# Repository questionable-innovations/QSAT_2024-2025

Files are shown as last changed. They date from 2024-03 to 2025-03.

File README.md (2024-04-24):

# APSS Reference PCBs
This is a collection of reference PCBs and Altium libraries for use within APSS.
The PSat folder includes a bunch of reference PCBs for use in PSat payloads.
The shared libraries folder includes a list of standardised parts for use within APSS. Many of these parts are available in the lab for breadboarding. You may of course use other components, but you will have to wait until they arrive before testing. 

## PSat Reference PCBs
A small collection of compatible PCBs and schematics for making a PSat payload with. See the separate readme in the folder for more details.

## APSS Altium Libraries
The libraries are split into flight-ready parts and prototyping parts. Prototyping parts are generally good parts that are cost-optimised, may not be automotive/military rated, and are not screened for CMOS latchups. These parts are useful for any non-critical design projects like PSat or ElevatorSat. 

Flight-ready parts are generally the highest performance parts that can be obtained for the role. They are automotive rated (or at least rated to automotive-like temperatures), checked for non-CMOS alternatives, etc. These should be used only for satellite-rated hardware like cubesat payloads, as some of these parts cost up to $20 each.

A General Components library also contains components like generic resistors, test points and pads, solder jumpers, etc.

## APSS Breadboard Adapters
A collection of small PCBs to use SMT parts on a breadboard.

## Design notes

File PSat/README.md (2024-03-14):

# PSat Reference PCBs
This is a collection of general-purpose PCBs for use in Psat payloads. This is designed to minimise the boilerplate that every PSat requires and allows you to specialise on whatever unique payload you choose.
Feel free to use this in your own payload. you could (in order of increasing complexity):

-   Use a previously assembled board, no work necessary
-   Assemble a board from an existing, unpopulated PCB and components (recommended)
-   Modify the PCB layout to suit your needs, print it, and assemble it
-   Use the schematic as a reference for your own custom design and layout
-   etc.

The original v1 and v2 designs were designed by Ross Porter (me), but I don’t expect this to be a static project: This is designed to be a community project, so once I’m gone I expect those with some electrical experience to take ownership, making adjustments or adding new features as required.

## Payload Slices
There are several boards that can be mixed and matched according to your needs. A brief description of each is given below. A full description can be found in the relevant subfolder's readme.

### Power Supply Unit (PSU)
The PSU slice is responsible for both charging the Lithium battery that powers your PSat, but also providing usable power rails for all your other devices. The board provides two step-down converters (default 1.8V and 3.3V) and one step-up converter (default 5V), all user-configurable during assembly. The battery can be charged using a USB-C or micro USB cable.

### Microcontroller (MCU)
The brains of the operation. A simple breakout board with programming header attached - never get stuck trying to program your microcontroller again! UART, SPI and I2C buses (among other pins) are broken out onto additional, optional stack headers for communication with other devices or slices.

### Beacon
Lost your PSat? Not any more. The beacon slice provides three locator devices:
 - A fully automatic audio beeper. This beeper produces a sharp chirp (100dB from 10cm away) every couple of seconds, which should be audible from about 50-100m away.
 - A 915MHz LoRa radio module. No radio license necessary, this radio can be used by a microcontroller to transmit a signal that you and a base station can use to triangulate the location of your payload. With a theoretical range of up to 2km (or 20km with a directional antenna on the base station), this radio is always an option. 
 - A self-contained GPS module. Use in combination with the LoRa radio and a microcontroller to broadcast your exact payload's GPS coordinates.

## Versioning
This project uses a form of semantic versioning to manage board interoperability:
ver X.Y.Z means version X, revision Y, patch Z.

The version X relates to both electrical and physical compatibility. Boards that share a major version X shall be physically and electrically compatible with eachother. If a change prevents a board from either physically mating (e.g. changing stack header location) or electrically interoperating (e.g. changing the location of the stack's ground pin) with other boards then this must be associated with an increase in version number.

The revision number Y relates to software-level changes. If a change does not affect physical or electrical interoperability but does require changing software (e.g. the location of two control pins have been swapped) then this must be associated with an increase in the revision number.

The patch number Z relates to internal bug fixes or additions to functionality. An increase in a board's patch number must be completely transparent to the wider stack, only adding additional functionality or solving issues/bugs internal to the board. Any already working stack shall continue to function (physically, electrically, and programmatically) even if one board receives a patch.

Examples:

PSU v1.0.0 <=/=> MCU v2.0.0

MCU v2.0.0 <=> Beacon v2.1.0, with software changes

MCU v2.2.0 <=> Beacon v2.2.37, with no software changes

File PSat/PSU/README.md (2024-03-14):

# Power Supply Unit (PSU)

See the documentation folder for version-specific readme's.

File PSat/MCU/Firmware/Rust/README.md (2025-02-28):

# How to use

Install Rust: https://www.rust-lang.org/learn/get-started

Install MSP430-GCC (installer or toolchain-only): https://www.ti.com/tool/MSP430-GCC-OPENSOURCE. Make sure it's on your PATH (or on Linux you can use `rustc-wrapper.sh`).

Then run the following commands:
`rustup install toolchain nightly`
`rustup component add rust-src --toolchain nightly`

You can now build the executable with `cargo build`. You can build in release mode with `cargo build --release`

(On Linux you will have to change the 'runner' line in `.cargo/config.toml` from `run.bat` to `run.sh`.)

# Flashing the board

Either use Code Composer Studio, under the 'flash' option click the dropdown and select the option that says 'select file to flash'. Point CCStudio to the binary at ./target/msp430-none-elf/release/apss_mcu_pcb_firmware

Alternatively, download uniflash from https://www.ti.com/tool/UNIFLASH#downloads. After installation open the program and either use auto-detect or input the board name (MSP430FR2355) manually. Click on 'standalone command-line' to generate a .zip file with all you need to flash the board.
Extract this folder so that dslite.bat is at `./uniflash/dslite.bat` within the project. 
After setting up uniflash you can flash the board by using `cargo run` or `cargo run --release`. (This also builds the project.)

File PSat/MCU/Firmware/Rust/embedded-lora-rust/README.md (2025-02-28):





# `embedded-lora`
`no-std`-compatible, opinionated drivers for some LoRa modems. Despite almost all modems supporting multiple radio
modulations, these drivers only implement LoRa. Furthermore, we currently only test the EU 868 MHz variants; other
variants may or may not work.

## `embedded-lora-rfm95`



dependency status (https://deps.rs/crate/embedded-lora-rfm95)

The [embedded-lora-rfm95](./rfm95/README.md) crate implements a driver for the popular RFM95 chips.

Currently supported features are:
- [x] Single RX
- [x] Single TX
- [x] Advanced LoRa modem configuration
- [x] SPI and modem register debugging
- [x] LoRa utils for AirTime computation

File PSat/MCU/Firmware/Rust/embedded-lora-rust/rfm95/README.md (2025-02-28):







dependency status (https://deps.rs/crate/embedded-lora-rfm95)

# `embedded-lora-rfm95`
A `no-std`-compatible, opinionated driver for the RFM95 LoRa modem. It only supports the LoRa mode, and has only been
tested with the EU 868 MHz ISM bands for now.

## Features
The crate supports the following optional `cargo` features:

### `fugit` (disabled by default)
The `fugit`-feature implements simple `From`/`Into`-conversions between the built-in frequency type and
[`fugit`'s](https://crates.io/crates/fugit) [`HertzU32` type](https://docs.rs/fugit/latest/fugit/type.HertzU32.html).
This is a comfort-feature only, and does not enable additional functionality.

### `debug` (disabled by default)
The `debug` feature enables some debug functionality, namely an SPI debug callback which can be used to log all SPI
transactions with the RFM95 modem, and provides some helper functions to dump the register state and FIFO contents. The
`debug` feature also disables the modem silicon revision check.

To use this feature, you __MUST__ implement this extern callback function in your crate (otherwise you'll get a cryptic
linker error):
```rust
extern "Rust" {
    /// A debug callback that is called for every SPI transaction
    /// 
    /// # About
    /// This function is called for every SPI transaction, where `operation` is the operation type (`0x00` for read,
    /// `0x80` for replace), `address` is the register address, and `input` and `output` are the values written and read
    /// respectively.
    fn embeddedrfm95_spidebug_AwiUzTRu(operation: u8, address: u8, input: u8, output: u8);
}
```

Example implementation:
```rust
/// The debug callback implementation for `embedded-rfm95`
#[no_mangle]
pub extern "Rust" fn embeddedrfm95_spidebug_AwiUzTRu(operation: u8, address: u8, input: u8, output: u8) {
    // Print the transaction to stdout
    println!("[SPI 0x{operation:02X} @[0x{address:02X}] tx:0x{input:02X} rx:0x{output:02X}");
}
```

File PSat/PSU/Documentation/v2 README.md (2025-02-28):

# Psat PSU PCB v2
The PSU PCB provides 1.8V, 3.3V, 5V rails and a raw battery voltage rail. The various supply rails can be always on, or controlled by software (see Functionality). USB-C and micro-USB connectors are present to charge the battery using a standard USB wall charger.
The supply rail voltages can be adjusted by changing the feedback resistor values. See the schematic for details.

## Functionality
### Controlling the Supply Rails
The PSU board offers two different control modes for each supply rail, controlled by the switches the S1 component: 
In the “ON” mode the relevant supply is always on. This is the simplest operating mode and no interaction with the enable pins are necessary. In this mode the enable pin is connected to Vraw via a 1.5k current-limiting resistor.

In the “OFF / SW control” mode, the supply defaults to off (pulled down by a 1Megohm resistor) but a microcontroller can enable the supply by pulling the enable pin high. If you want to programmatically enable a supply during operation you need to use this mode and connect your microcontroller to the enable pins on the header. See ‘Connections’ for the exact voltage(s) required to enable each supply.

*Note: If you configure S1 into the “ON” mode and have also connected the enable pin to a microcontroller, make sure to leave that GPIO pin as an input pin, as otherwise you will waste power through the 1.5k resistor.*

### USB charging
The board is capable of charging a lithium-ion battery by connecting a USB charger.
The two USB connectors (USB-C and micro-USB) are provided for convenience. DO NOT CHARGE USING BOTH CONNECTORS AT ONCE.
The battery will charge up to 800mA (USB power supply willing). This rate can be decreased by changing the value of R6, according to the datasheet of the battery charger.

### Disable while charging
The final S1 switch (labelled '*' on the PCB) is the 'supply disabled while charging' switch. It determines whether all the supply rails (including Vraw) are available while a USB cable is plugged in. The battery will of course charge faster if the load is disabled during charging. The BQ21040 battery charger IC states that it can also power loads during charging, so long as the charging time does not exceed 10 hours as a result, but this is not universally true for all charging ICs. When this switch is set to "ON" the load is disabled during charging. When it is set to "SW control" the supplies are enabled even while plugged in.

### 'Remove Before Flight’ Connector
RBF is a connector that controls whether the battery is connected to the PSU and stack. When the jumper is removed the entire stack has no power. When a jumper is placed across ABF (shorting the two pins) the battery is disconnected to the PSU and hence the stack. It is placed at a right-angle so that the jumper may be removed prior to launch through a hole in the exterior PSat shell.

## Connections
Header H1:

 - 1V8 -  1.8V step-down supply rail, capable of 2A output, battery not withstanding.
 - 3V3 -  3.3V step-down supply rail, capable of 2A output, battery not withstanding. *
 - 5V  -  5V step-up supply rail, capable of 2A output, battery not withstanding.
 - GND -  Common ground for all supply rails.
 - Vraw - Raw battery voltage. For a Li-ion battery this is between ~4.2V and ~3V.
 - 1V8_PG - Power good indicator for the 1.8V rail. Open-drain output: While the output voltage is more than 20% away from the regulation level this pin is pulled low, otherwise it is floating - you should attach this to a voltage source via a pullup resistor of your choosing.
 - 3V3_PG - Power good indicator for the 3.3V rail. Open-drain output: While the output voltage is more than 20% away from the regulation level this pin is pulled low,  otherwise it is floating - you should attach this to a voltage source via a pullup resistor of your choosing.
 - EN_1V8 - This pin may be pulled up above 1.5V to enable the 1.8V supply. The pin has a 1 Megohm pulldown resistor attached. When the equivalent S1 switch is in the "ON" position a 1.5k pullup resistor pulls this pin up to Vraw.
 - EN_3V3 - This pin may be pulled up above 1.5V to enable the 3.3V supply. The pin has a 1 Megohm pulldown resistor attached. When the equivalent S1 switch is in the "ON" position a 1.5k pullup resistor pulls this pin up to Vraw.
 - EN_5V - This pin may be pulled up above 1.2V to enable the 5V supply. The pin has a 1 Megohm pulldown resistor attached. When the equivalent S1 switch is in the "ON" position a 1.5k pullup resistor pulls this pin up to Vraw.

 \* *Note: This voltage is only stepped-down from the battery voltage, so if that goes below 3.3V this supply rail will as well. This means that across a full battery discharge this rail is nominally between 3.3V - 3.0V.*

## PCB Stacking
The PSat PSU is designed to be used in conjunction with either a single payload PCB (i.e. ‘2 PCB stack’) or in a stack of multiple PCBs (‘Multi-PCB stack’).

There are three types of 2.54mm pitch headers available in the lab, and which the PCB was designed with in mind:
Male headers with a 6mm mating length, 2.54mm insulation and a 3mm post.
Female headers with 8.5mm insulation and a 3mm post.
'Arduino female stacking headers' with 8.5mm of insulation, and 10.5mm posts.
### 2 PCB Stack
The simplest stack uses the supplied female header on the payload PSU and regular male headers on the payload board, pointed down. This produces a stack height of about 5mm.

The PSU is designed to go at the bottom of the stack (hence why the example payload has a cutout for the battery), but it can be moved up in the stack provided the battery can fit in the remaining space.

If a larger stack height is needed the standard female headers can be used to grant either ~8.5mm or ~11mm stack height (depending on whether the male pins are soldered with the plastic insulation between the PCBs or on the other side).

The stack height can be eliminated entirely if the male header is soldered such that the insulation is not between the two PCBs. Note that this would require the PSU PCB to be flipped (reversing the order of the header H1), as the underside of the PSU PCB must be used to mate against the payload (as no components on this side to interfere).

### Multi-PCB stack
The simplest stack uses the female stacking headers for each layer, except for the bottom which can use a standard female header, and the top which can use a standard male header (pointing down). This enforces a board-to-board stack height of 11mm between payload boards, and a stack height of around 5mm between the PSU board and the first payload board.

## Future changes
Maybe add a resettable fuse between the two USB connector’s bus voltages?

Maybe add a polyfuse to battery and each rail’s outputs

## Version History + Changelog
Version 2 - Not yet printed.
Move away from a centralised, fixed-size stack header to a flexible ‘only-what-is-necessary’ header: Rather than using a single 30-pin header with many unused pins, we use only a 10-pin header because the PSU PCB only needs 10 pins. Removed unused header pins as a result. PCBs further above in the stack can add additional headers adjacent to ours if necessary. 
Also switched to 2.54mm header due to a lack of 1.27mm ‘stacking’ headers. 2.54mm headers are also easier to route around, which actually makes it easier to add more pins to other PCBs in the stack if necessary, even though they’re bigger. 
Fixed Q1 by swapping pins 2 and 3. The mosfet body diode allowed Vbat to power the load even when the mosfet was (supposed to be) acting as an open circuit.
Added a resistor between Vraw and the EN_XYZ pins to prevent possible short circuit with microcontroller if switch is improperly configured

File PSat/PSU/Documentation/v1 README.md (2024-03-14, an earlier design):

# Psat PSU PCB v1
The PSU PCB provides 1.8V, 3.3V, 5V rails and a raw battery voltage rail. The various supply rails can be enabled, or controlled by software (see Functionality). USB-C and micro-USB connectors are present to charge the battery using a standard USB wall charger.
## Functionality
### Controlling the Supply Rails
The PSU board offers two different control modes for each supply rail, controlled by the switches on the S1 component: 
In the “ON” mode the relevant supply is always on. This is the simplest operating mode and no interaction with the enable pins are necessary. The enable pin is shorted to Vraw in this mode.

In the “OFF / SW control” mode, the supply defaults to off (pulled down by a 1Megohm resistor) but a microcontroller can enable the supply by pulling the enable pin high. If you want to programmatically enable a supply during operation you need to use this mode and connect your microcontroller to the enable pins on the header. See ‘Connections’ for the exact voltage(s) required to enable each supply.

**NOTE**: *If you have connected a microcontroller to the EN pins and plan to use it to control the supplies then a misconfigured S1 switch could result in your microcontroller trying to fight against an enable pin shorted to Vraw. Instead of using your GPIO as an output pin, we suggest setting it as an input pin and toggling the state of the internal pullup resistor to control the supplies. When the internal pullup is enabled it will form a voltage divider with the 1 Megohm external resistor, but it should be more than enough to activate the supply. In the case that S1 is misconfigured (i.e. in the “ON” mode, shorting the enable pin to Vraw) the pullup resistor will limit current to safe levels. See below.*

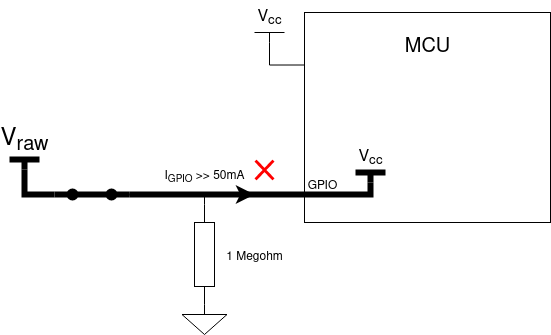
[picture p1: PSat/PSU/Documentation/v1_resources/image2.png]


A misconfiguration when controlling via an output pin can cause a short.

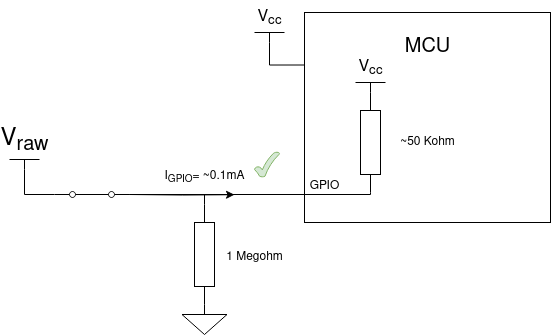
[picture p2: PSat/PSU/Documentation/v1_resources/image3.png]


Using an input pin with a pullup resistor enabled will limit current to a safe value even when misconfigured…

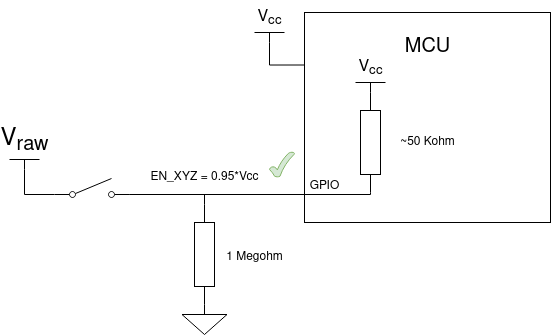
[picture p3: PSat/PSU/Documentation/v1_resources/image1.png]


…while still allowing control when correctly configured.

### USB charging
The two USB connectors (USB-C and micro-USB) are provided for convenience. **DO NOT PLUG IN TWO CABLES AT ONCE**.
The battery will charge at a rate of 800mA. This rate can be decreased by changing the value of R6, according to the datasheet of the battery charger.

### Disable while charging
The final S1 switch (labelled '*' on the PCB) is the 'supply disabled while charging' switch. It determines whether all the supply rails (including Vraw) are available while a USB cable is plugged in. The battery will of course charge faster if the load is disabled during charging. The BQ21040 battery charger IC states that it can also power loads during charging, so long as the charging time does not exceed 10 hours as a result, but this is not universally true for all charging ICs. When this switch is set to "ON" the load is disabled during charging. When it is set to "SW control" the supplies are enabled even while plugged in.

**NOTE**: *This feature does not work as intended on the v1 board. When set to ‘ON’ the payload continues to be powered with a voltage source about 0.7V lower than the battery voltage. It can either be fixed by mounting Q1 such that pins 2 and 3 are swapped, or if the functionality is not required then the ‘disable while charging’ switch can be left in the ‘OFF / SW control’ setting.*

### 'Attach Before Flight’ Connector
ABF is a connector that controls whether the battery is connected to the PSU and stack. When the jumper is removed the entire stack has no power. When a jumper is placed across ABF (shorting the two pins) the battery is connected to the PSU and hence the stack. It is placed at a right-angle so that the jumper may be inserted prior to launch through a hole in the exterior PSat shell.

## Connections
Header H1:

- 1V8 -  1.8V supply rail, capable of 2A output.
- 3V3 -  3.3V supply rail, capable of 2A output.
- 5V  -  5V supply rail, capable of 2A output.
- GND -  Common ground for all supply rails.
- Vraw - Raw battery voltage. For a Lithium battery this is between 3V to 4.2V.
- 1V8_PG - Power good indicator for the 1.8V rail. Open-drain output. It is is pulled up to Vraw when the output voltage is within 20% of the regulation level, otherwise it is low.
- 3V3_PG - Power good indicator for the 3.3V rail. Open-drain output. It is is pulled up to Vraw when the output voltage is within 20% of the regulation level, otherwise it is low.
- EN_1V8 - When the equivalent S1 switch is set to "SW control", this pin is pulled down with a 1 Megohm resistor. It may be pulled up above 1.5V to enable the 1.8V supply. When the equivalent S1 switch is in the "ON" position this pin is shorted to Vraw.
- EN_3V3 - When the equivalent S1 switch is set to "SW control", this pin is pulled down with a 1 Megohm resistor. It may be pulled up above 1.5V to enable the 3.3V supply. When the equivalent S1 switch is in the "ON" position this pin is shorted to Vraw.
- EN_5V  - When the equivalent S1 switch is set to "SW control", this pin is pulled down with a 1 Megohm resistor. It may be pulled up above 1.2V to enable the 5V supply. When the equivalent S1 switch is in the "ON" position this pin is shorted to Vraw.

## PCB Stacking
The PSat PSU is designed to be used in conjunction with a single payload PCB (or in a larger stack, provided you can find a female header with long enough posts).

The stack height with the connector given in the Altium project is 6.6mm, though this is just a placeholder. The connector is a board-to-board connector and is designed to be soldered in place, rendering the two PCBs permanently attached. We recommend finding another header, particularly if you want more than one payload PCB.

## Future changes
The S1 switches being inaccessible in small stack heights is inconvenient. Potentially replace with a right-angle connector?

Maybe add a resettable fuse between the two USB connector’s bus voltages?

Instead of S1 shorting the EN pin to Vraw, put a resistor (1k?) between potential MCUs and the EN line to prevent the possibility of shorts when misconfigured.

To check: The ‘power good’ indicators may need a pull-up resistor.

## PCB Version History
Version 1 - Initial design. Printed January 2024.

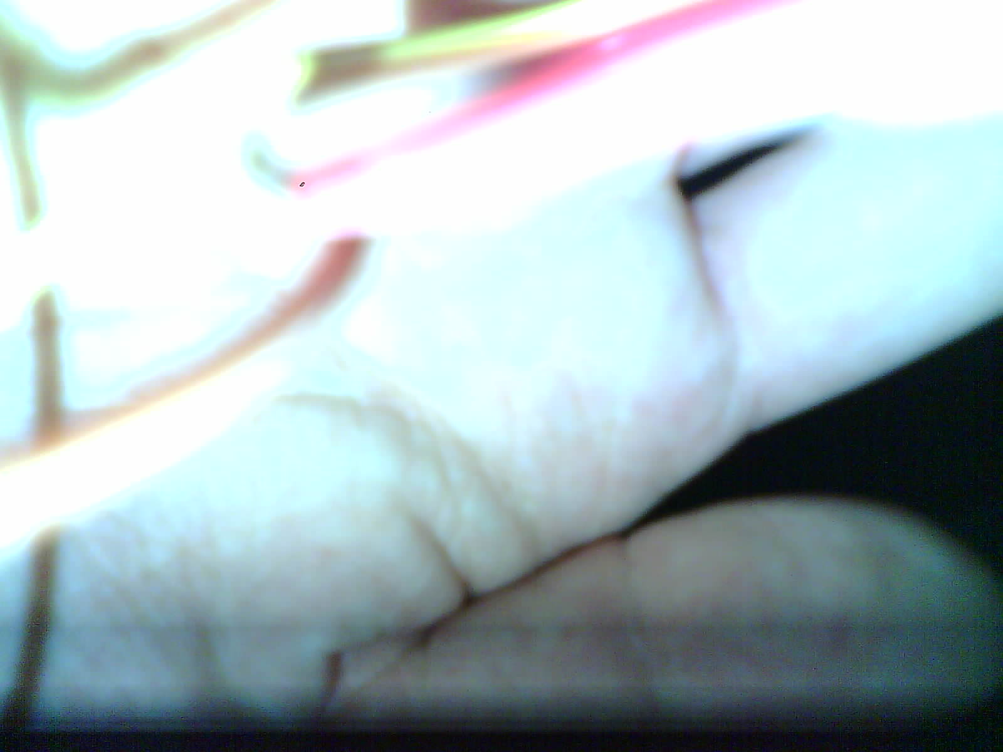
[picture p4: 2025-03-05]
ESPCAM/photos/picture45.jpg

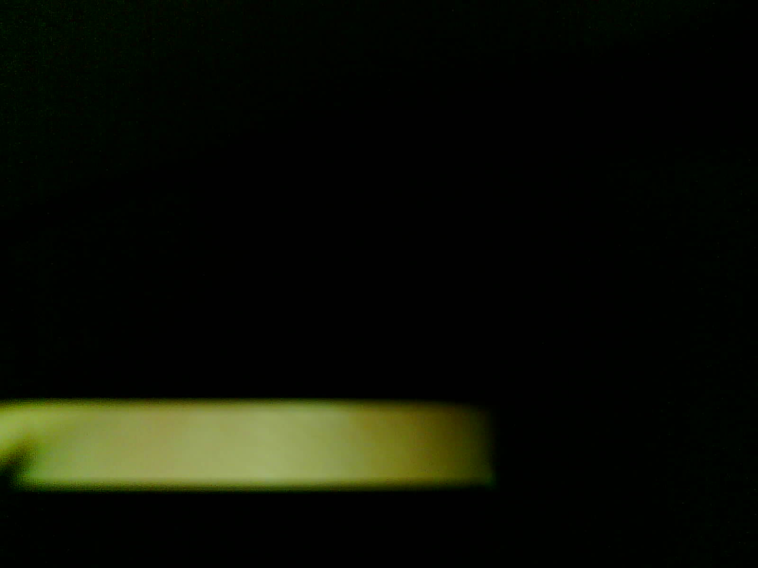
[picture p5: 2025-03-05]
ESPCAM/photos/picture4.jpg

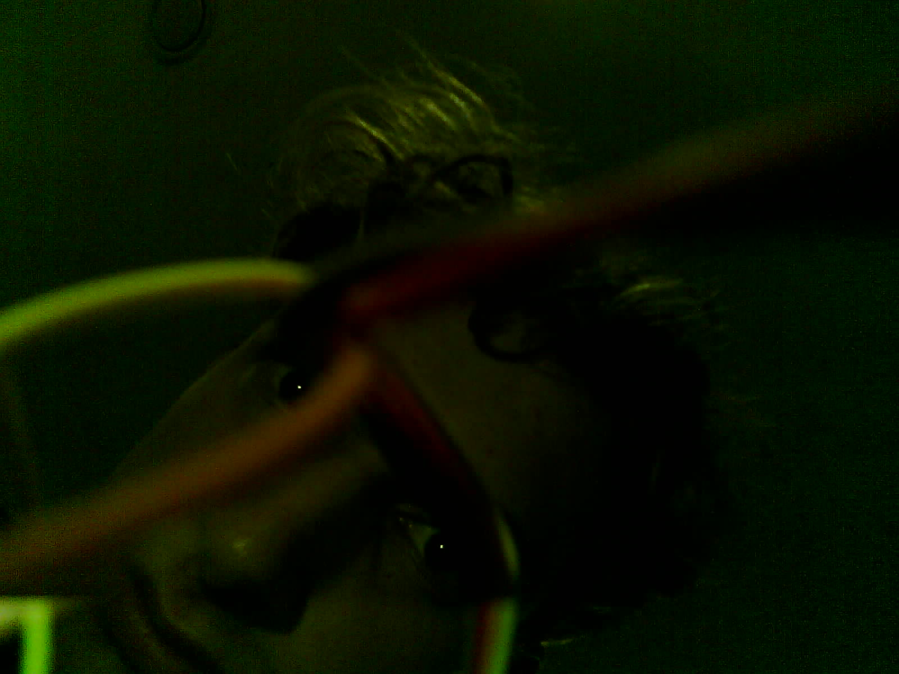
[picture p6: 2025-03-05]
ESPCAM/photos/picture10.jpg

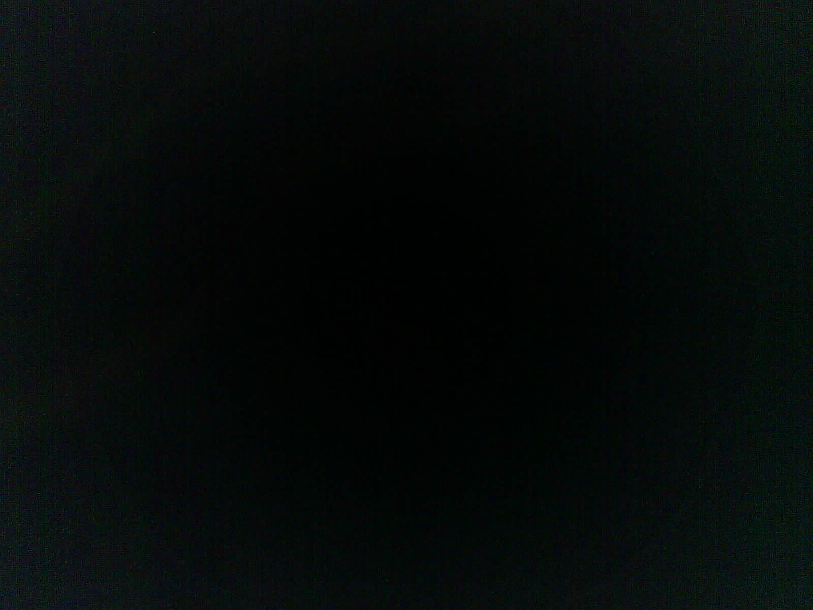
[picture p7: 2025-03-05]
ESPCAM/photos/picture37.jpg

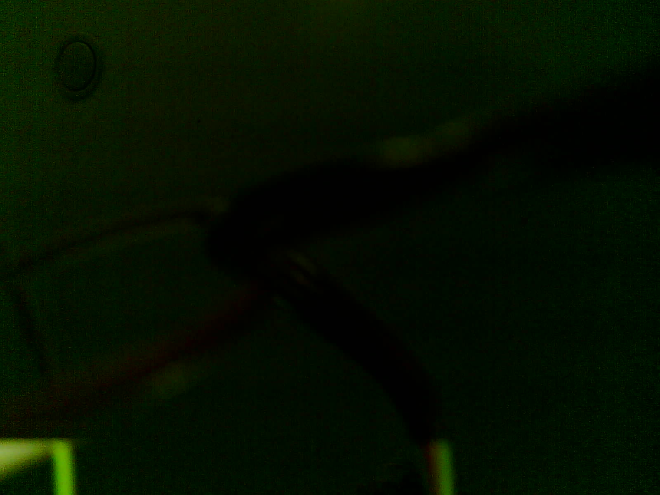
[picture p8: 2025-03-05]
ESPCAM/photos/picture9.jpg

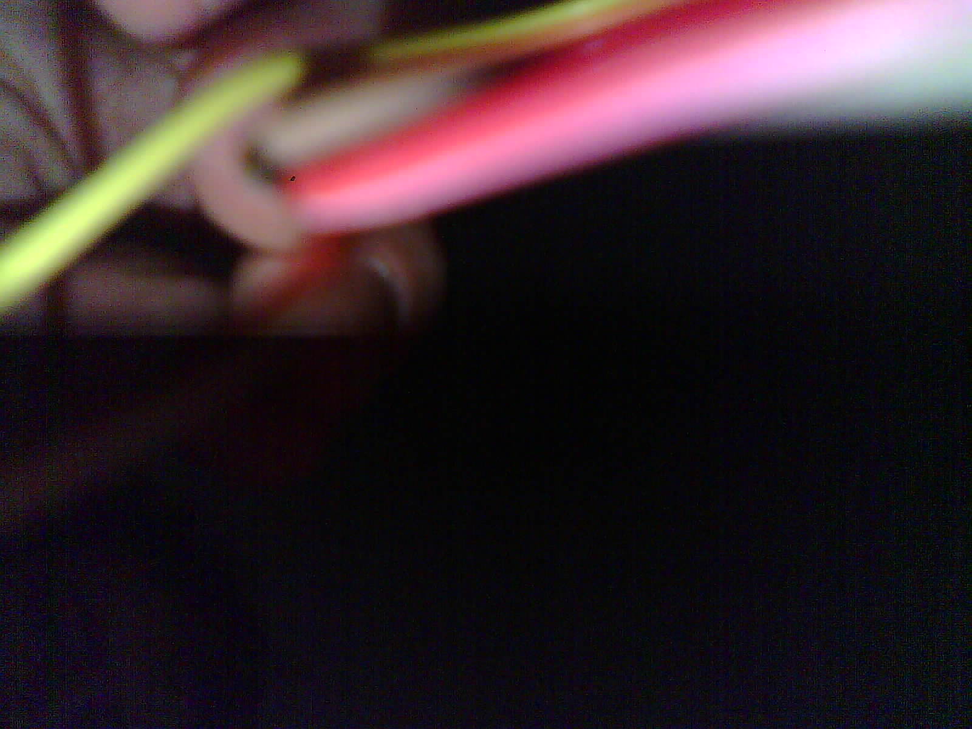
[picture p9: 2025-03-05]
ESPCAM/photos/picture39.jpg

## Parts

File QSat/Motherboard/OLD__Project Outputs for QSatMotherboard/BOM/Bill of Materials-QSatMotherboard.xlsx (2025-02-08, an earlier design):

Designator | Description | Comment | MF Part No. | Quantity | Supplier 1 | Supplier 1 Part No. | Package | APSS Standard Part
50k | Passive - Resistor Series, 0805, 0.5%, 10 - 1M, E24, 0.063W, 1/8W, ±25ppm/°C, -55°C ~ 155°C, 0805 (2012 Metric) | =Value |  | 1 | Digikey |  | 0805 | APSS Standard
ANT1 | Spring Antenna | HP-915-2.5A-9T | HP-915-2.5A-9T | 1
C1, C3, C4, C13, CIMU, CIMU1 | Generic Capacitor | 100nF | C0805C104K5RAC7800 | 6 | Digikey | 399-C0805C104K5RAC7800CT-ND | 0805
C2, C11, C12 | Passive - Capacitor, X5R, 22uF Max, 6.3V, 0805 (2012 Metric), ±20%, -55°C ~ 85°C. 8.8uF @ 5V | 22uF | C0805C226M9PACTU | 3 | Digikey | 399-C0805C226M9PAC7800CT-ND | 0402 | APSS Standard
C5 | Generic Capacitor | 1nF | 399-C0805C102J5GAC7800CT-ND | 1 | Digikey | 399-C0805C102J5GAC7800CT-ND | 0805
C10 | Passive - Capacitor, X7R, 220nF Max, 100V, 0805 (2012 Metric), ±10%, -55°C ~ 85°C. 200nF @ 10V, 110nF @ 50V, 55nF @ 100V | 220nF | C0805C224K1RAC7800 | 1 | Digikey | 399-C0805C224K1RAC7800CT-ND | 0805 | APSS Standard
D1, D4 | Diode - LED, 0603 | LTST-C190 Series | LTST-C190KGKT | 2 | Digikey |  | 0603 | APSS Standard
D2 | Diode - LED, 0603 | LTST-C190 Series | LTST-C190KSKT | 1 | Digikey |  | 0603 | APSS Standard
D3 | Diode - LED, 0603 | LTST-C190 Series | LTST-C190KAKT | 1 | Digikey |  | 0603 | APSS Standard
D5 | Diode - Low Reverse Leakage, 1.25 Vf @ 150 mA, 1 µA Reverse @ 75 V, SOD-123 | 1N4148W-TP | 1N4148W-TP | 1 | Digikey | 1N4148WTPMSCT-ND | SOD-123 | APSS Standard
H4 | Header - Picoblade 02-pin, TH, STR | 0530470210 | 0530470210 | 1 | Digikey | 530470210 |  | APSS Standard
J1 | No Description Available | PPTC081LFBN-RC |  | 1
J1b | Header - Picoblade 08-pin, SMT, RA | 0532610871 | 0532610871 | 1 | Digikey | WM7626CT-ND |  | APSS Standard
J2 | No Description Available |  |  | 1
J3, MH1, MH2 | Header - Picoblade 03-pin, TH, STR | 0530470310 | 0530470310 | 3 | Digikey | WM1732-ND |  | APSS Standard
LS1 | 8.5 mm, 5 Vo-p, 100 dB, Surface Mount (SMT), Magnetic Audio Transducer Buzzer | CMT-8504-100-SMT-TR | CMT-8504-100-SMT-TR | 1
OP1 | IC - Opamp, Precision, 2-Channel, Zero Drift, 270kHz GBWP, RRIO, 1.8V to 5.5V, -40 to 125, 8-MSOP | NCS2333DMR2G | NCS2333DMR2G | 1 | Digikey | 488-NCS2333DMR2GCT-ND | MSOP-8 0.65mm | APSS Standard
PWR | Header - Picoblade 02-pin, TH, STR | 0530470210 |  | 1 | Digikey | 530470210 |  | APSS Standard
Q1 | Transistor - MOSFET, N-Channel AS2312 | AS2312 | AS2312 | 1 | Digikey | 4530-AS2312CT-ND | SOT23-3 | APSS Standard
Q2 | Transistor - MOSFET, P-Channel SSM3J328R,LF | SSM3J328R,LF | SSM3J328R,LF | 1 | Digikey | SSM3J328RLFCT-ND | SOT23-3 | APSS Standard
R1 | Passive - Resistor Series, 0805, 5%, 100m - 22M, E24, 0.063W, 1/16W, ±200ppm/°C, -55°C ~ 155°C, 0805 (2012 Metric) | 47k | RMCF0805JT39K0 | 1 | Digikey |  | 0805 | APSS Standard
R2, R3, R4, R13, R16, R24, R25 | Passive - Resistor Series, 0805, 5%, 100m - 22M, E24, 0.063W, 1/16W, ±200ppm/°C, -55°C ~ 155°C, 0805 (2012 Metric) | 1k | RMCF0805JT1K00 | 7 | Digikey |  | 0805 | APSS Standard
R5 | Passive - Resistor Series, 0805, 5%, 100m - 22M, E24, 0.063W, 1/16W, ±200ppm/°C, -55°C ~ 155°C, 0805 (2012 Metric) | 47k | RMCF0805JT147K0 | 1 | Digikey |  | 0805 | APSS Standard
R6 | Passive - Resistor Series, 0805, 5%, 100m - 22M, E24, 0.063W, 1/16W, ±200ppm/°C, -55°C ~ 155°C, 0805 (2012 Metric) | 47k | RMCF0805JT47K0 | 1 | Digikey |  | 0805 | APSS Standard
R7 | Passive - Resistor Series, 0805, 5%, 100m - 22M, E24, 0.063W, 1/16W, ±200ppm/°C, -55°C ~ 155°C, 0805 (2012 Metric) | 4.7k | RMCF0805JT4K70 | 1 | Digikey |  | 0805 | APSS Standard
R8, R10, R27 | Passive - Resistor Series, 0805, 5%, 100m - 22M, E24, 0.063W, 1/16W, ±200ppm/°C, -55°C ~ 155°C, 0805 (2012 Metric) | 10k | RMCF0805JT4K70 | 3 | Digikey |  | 0805 | APSS Standard
R9, R11 | Passive - Resistor Series, 1206, 0.5%, 1R - 2M, E24+E96, 0.52W, 1/2W, ±25ppm/°C, -55°C ~ 155°C, 0805 (3216 Metric) | 2 | TNPW1206xxxxDE | 2 | Digikey |  | 0805 | APSS Standard
R12 | Passive - Resistor Series, 1206, 0.5%, 1R - 2M, E24+E96, 0.52W, 1/2W, ±25ppm/°C, -55°C ~ 155°C, 0805 (3216 Metric) | 50m | TNPW1206xxxxDE | 1 | Digikey |  | 0805 | APSS Standard
R14 | Passive - Resistor Series, 0805, 5%, 100m - 22M, E24, 0.063W, 1/16W, ±200ppm/°C, -55°C ~ 155°C, 0805 (2012 Metric) | 130 | RMCF0805JT1K00 | 1 | Digikey |  | 0805 | APSS Standard
R15 | Passive - Resistor Series, 0805, 5%, 100m - 22M, E24, 0.063W, 1/16W, ±200ppm/°C, -55°C ~ 155°C, 0805 (2012 Metric) | 150 | RMCF0805JT1K00 | 1 | Digikey |  | 0805 | APSS Standard
R17 | Passive - Resistor Series, 0805, 5%, 100m - 22M, E24, 0.063W, 1/16W, ±200ppm/°C, -55°C ~ 155°C, 0805 (2012 Metric) | 600 | RMCF0805JT1K00 | 1 | Digikey |  | 0805 | APSS Standard
R21, R22, R23 | Passive - Resistor Series, 0805, 5%, 100m - 22M, E24, 0.063W, 1/16W, ±200ppm/°C, -55°C ~ 155°C, 0805 (2012 Metric) | 180k | RMCF0805JT180K | 3 | Digikey |  | 0805 | APSS Standard
R26 | Passive - Resistor Series, 0805, 5%, 100m - 22M, E24, 0.063W, 1/16W, ±200ppm/°C, -55°C ~ 155°C, 0805 (2012 Metric) | 39k | RMCF0805JT39K0 | 1 | Digikey |  | 0805 | APSS Standard
S1 | Switch - Slide, SPDT, Straight, Break Before Make, 300mA, 6V | JS102011JCQN | JS102011JCQN | 1 | Digikey | CKN10721CT-ND |  | APSS Standard
U1 |  | MSP430FR2355TPT | MSP430FR2355TPT | 1 | Digikey | 296-50260-ND | LQFP-48
U2 | IMU ACCEL/GYRO I2C/SPI 14LGA | LSM6DSMTR |  | 1 |  |  | LGA-14L-DM00249496
U3 | CD-PA1616D GNSS patch antenna module | CD-PA1616D | CD-PA1616D | 1
U4 | LoRa transceiver | LORA127X-C1 | LORA127X-C1 | 1

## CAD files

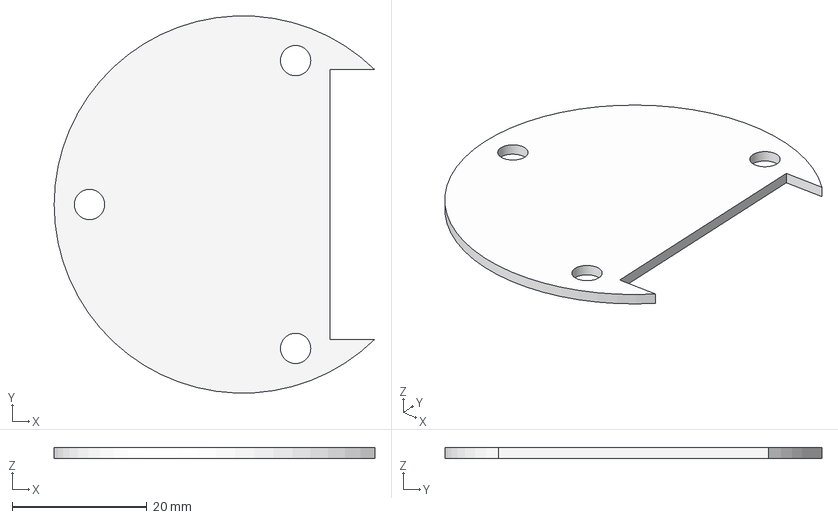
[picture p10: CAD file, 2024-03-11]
QSat/Motherboard/Payload Outline.step
47.6 x 56.0 x 1.60 mm

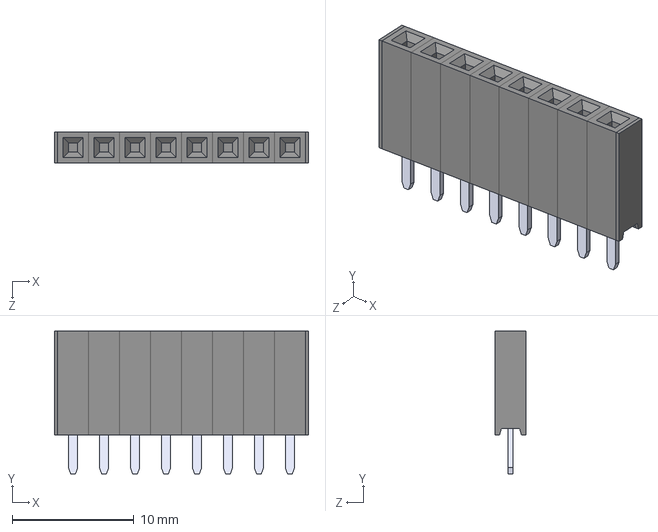
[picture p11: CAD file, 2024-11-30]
QSat/PartLib/PPTC081LFBN-RC/PPTC081LFBN-RC.STEP
20.8 x 11.7 x 2.54 mm
PPPC021LFBN-RC_C08
Pin - Tin x 8

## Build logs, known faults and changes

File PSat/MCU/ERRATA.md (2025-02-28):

# ERRATA
## 'Unknown device' when using 2-wire programming
Despite being the value recommended in the datasheet, C5 being 1nF is sometimes too high to allow programming when using 2-wire mode. Reducing C5 to 470pF solved the issue.

Affects: All versions

Fixed in version: TBD

## Reset pullup resistor value
Pullup resistor R1 is wrongly valued at 4.7k, the datasheet recommends 47k. No adverse affects noted. 

Affects v2.0.0 - v2.0.2

Fixed in: v2.0.3

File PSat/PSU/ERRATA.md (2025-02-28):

# ERRATA

## 'Remove/Attach Before Flight' header wrongly documented
The header that controls whether the payload switches on was originally an 'attach before flight' connector. This was changed to a 'remove before flight' header in v2.0.3, but the documentation was not updated until v2.0.6. The header behaves as an 'attach before flight' header from v2.0.0 to v2.0.2, and as a 'remove before flight' header from v2.0.3 onwards.

Affects: v2.0.3 - v2.0.5

Fixed in version: v2.0.6

## 'Disable while charging' feature does not work
The 'disable while charging' feature doesn't work correctly on the v1 PSU board. The toggle switch for this should be left in the 'Off / SW Control' position, unless the following fix is applied: Resolder Q1 such that pins 2 and 3 are swapped.

Affects: v1.*

Fixed in version: v2.0.0

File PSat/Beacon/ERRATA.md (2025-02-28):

# ERRATA

## GPS Enable Polarity
The documented functionality of the GPS enable transistor (Q2) is inverted: The documentation wrongly states that setting the gate of Q2 high enables the GPS. The gate of Q2 must be set *low* to enable the GPS. 

This also affects the default setting of SB7. The GPS defaults to being off with the default configuration, unless SB2 is shorted and GPS_EN is controlled as mentioned above.

Affects: v2.0.0 - v2.0.2

Fixed in version: v2.0.3

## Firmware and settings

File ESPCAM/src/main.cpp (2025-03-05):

#include "esp_camera.h"
#include "Arduino.h"
#include "FS.h"                // SD Card ESP32
#include "SD_MMC.h"            // SD Card ESP32
#include "soc/soc.h"           // Disable brownour problems
#include "soc/rtc_cntl_reg.h"  // Disable brownour problems
#include "driver/rtc_io.h"
#include <EEPROM.h>            // read and write from flash memory

// define the number of bytes you want to access
#define EEPROM_SIZE 16

// Pin definition for CAMERA_MODEL_AI_THINKER
#define PWDN_GPIO_NUM     32
#define RESET_GPIO_NUM    -1
#define XCLK_GPIO_NUM      0
#define SIOD_GPIO_NUM     26
#define SIOC_GPIO_NUM     27

#define Y9_GPIO_NUM       35
#define Y8_GPIO_NUM       34
#define Y7_GPIO_NUM       39
#define Y6_GPIO_NUM       36
#define Y5_GPIO_NUM       21
#define Y4_GPIO_NUM       19
#define Y3_GPIO_NUM       18
#define Y2_GPIO_NUM        5
#define VSYNC_GPIO_NUM    25
#define HREF_GPIO_NUM     23
#define PCLK_GPIO_NUM     22

int pictureNumber = 0;

void setup() {
  WRITE_PERI_REG(RTC_CNTL_BROWN_OUT_REG, 0); //disable brownout detector
 
  Serial.begin(115200);
  //Serial.setDebugOutput(true);
  //Serial.println();
  
  camera_config_t config;
  config.ledc_channel = LEDC_CHANNEL_0;
  config.ledc_timer = LEDC_TIMER_0;
  config.pin_d0 = Y2_GPIO_NUM;
  config.pin_d1 = Y3_GPIO_NUM;
  config.pin_d2 = Y4_GPIO_NUM;
  config.pin_d3 = Y5_GPIO_NUM;
  config.pin_d4 = Y6_GPIO_NUM;
  config.pin_d5 = Y7_GPIO_NUM;
  config.pin_d6 = Y8_GPIO_NUM;
  config.pin_d7 = Y9_GPIO_NUM;
  config.pin_xclk = XCLK_GPIO_NUM;
  config.pin_pclk = PCLK_GPIO_NUM;
  config.pin_vsync = VSYNC_GPIO_NUM;
  config.pin_href = HREF_GPIO_NUM;
  config.pin_sccb_sda = SIOD_GPIO_NUM;
  config.pin_sccb_scl = SIOC_GPIO_NUM;
  config.pin_pwdn = PWDN_GPIO_NUM;
  config.pin_reset = RESET_GPIO_NUM;
  config.xclk_freq_hz = 20000000;
  config.pixel_format = PIXFORMAT_JPEG; 
  
  if(psramFound()){
    config.frame_size = FRAMESIZE_UXGA; // FRAMESIZE_ + QVGA|CIF|VGA|SVGA|XGA|SXGA|UXGA
    config.jpeg_quality = 10;
    config.fb_count = 2;
  } else {
    config.frame_size = FRAMESIZE_SVGA;
    config.jpeg_quality = 12;
    config.fb_count = 1;
  }
  
  // Init Camera
  esp_err_t err = esp_camera_init(&config);
  if (err != ESP_OK) {
    Serial.printf("Camera init failed with error 0x%x", err);
    return;
  }
  
  //Serial.println("Starting SD Card");
  if(!SD_MMC.begin()){
    Serial.println("SD Card Mount Failed");
    return;
  }
  
  uint8_t cardType = SD_MMC.cardType();
  if(cardType == CARD_NONE){
    Serial.println("No SD Card attached");
    return;
  }

  // force flash off
  // pinMode(4, OUTPUT);
  // digitalWrite(4, LOW);
  // rtc_gpio_hold_en(GPIO_NUM_4);
  
  while (true) {
    camera_fb_t * fb = NULL;
    
    // Take Picture with Camera
    fb = esp_camera_fb_get();  
    if(!fb) {
      Serial.println("Camera capture failed");
      return;
    }
    // initialize EEPROM with predefined size
    EEPROM.begin(EEPROM_SIZE);
    pictureNumber = EEPROM.read(0) + 1;

    // Path where new picture will be saved in SD Card
    String path = "/picture" + String(pictureNumber) +".jpg";
    // String path = "/picture" + String(millis()) + ".jpg";

    fs::FS &fs = SD_MMC; 
    Serial.printf("Picture file name: %s\n", path.c_str());
    
    File file = fs.open(path.c_str(), FILE_WRITE);
    if(!file){
      Serial.println("Failed to open file in writing mode");
    } 
    else {
      file.write(fb->buf, fb->len); // payload (image), payload length
      Serial.printf("Saved file to path: %s\n", path.c_str());
      EEPROM.write(0, pictureNumber);
      EEPROM.commit();
    }
    file.close();
    esp_camera_fb_return(fb); 

    delay(1000); // Add a delay to avoid taking pictures too quickly
  }
  
}

void loop() {
  
}

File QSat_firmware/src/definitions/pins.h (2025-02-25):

#pragma once
#include <Arduino.h>

// 1	P1.2	I/O	LVCMOS	DVCC	OFF	TRUE	LoRa	SPI Master Out
// 2	P1.1	I/O	LVCMOS	DVCC	OFF	TRUE	LoRa	SPI Clock
// 8	P2.7	I/O	LVCMOS	DVCC	OFF	TRUE	LoRa	Lora Reset
// 9	P2.6	I/O	LVCMOS	DVCC	OFF	TRUE	LoRa	LoRa IRQ (DIO0)
// 10	P2.5	I/O	LVCMOS	DVCC	OFF	TRUE	LoRa	LoRa Configurable DIO1 (RadioLib wants it?)
// 11	P2.4	I/O	LVCMOS	DVCC	OFF	TRUE	ESP32 Cam	Hopefully will be used for OneWire commication with the ESPCam
// 12	P4.7	I/O	LVCMOS	DVCC	OFF	TRUE	Accelerometer	LSM6DSMTR I2C SCL
// 13	P4.6	I/O	LVCMOS	DVCC	OFF	TRUE	Accelerometer	LSM6DSMTR I2C SDA
// 23	P4.3	I/O	LVCMOS	DVCC	OFF	TRUE	GPS Module	GPS TX
// 24	P4.2	I/O	LVCMOS	DVCC	OFF	TRUE	GPS Module	GPS RX
// 27	P2.3	I/O	LVCMOS	DVCC	OFF	TRUE	GPS Module	GPS Enable
// 29	P2.1(RD)	I/O	LVCMOS	DVCC	OFF	TRUE	CamTrigServo	Send trigger servo PWM signal
// 30	P2.0	I/O	LVCMOS	DVCC	OFF	TRUE	CamTrigServo	Shutter reload servo PWM signal
// 31	P1.7	I/O	LVCMOS	DVCC	OFF	FALSE	JTAG, ESP32 Cam	Dual Use - It's a backup for the ESPCam com. If the DIY OneWire protocol doesn't work, we'll jank together the serial logs with communication to the ESPCam.
// 40	P5.3	I/O	LVCMOS	DVCC	OFF	TRUE	Current Sense	Analog current sense for servo controlling the shutter
// 41	P5.2	I/O	LVCMOS	DVCC	OFF	TRUE	LightSense	Read the photoresiste to detect leaving the capsual
// 42	P5.1	I/O	LVCMOS	DVCC	OFF	TRUE	Buzzer	PWM output for the buzzer - useful for finding capsual after rocket launch
// 43	P5.0	I/O	LVCMOS	DVCC	OFF	TRUE	Batt Manage	Default Sense Design
// 44	P3.3	I/O	LVCMOS	DVCC	OFF	TRUE	Status LED	LED1
// 45	P3.2	I/O	LVCMOS	DVCC	OFF	TRUE	Status LED	LED2
// 46	P3.1	I/O	LVCMOS	DVCC	OFF	TRUE	Status LED	LED3
// 47	P3.0	I/O	LVCMOS	DVCC	OFF	TRUE	Batt Manage	5V Enable
// 48	P1.3	I/O	LVCMOS	DVCC	OFF	TRUE	LoRa	SPI Master In

const int LoRa_SPI_SCK = P1_1;
const int LoRa_SPI_MOSI = P1_2;
const int LoRa_SPI_MISO = P1_3;
const int LoRa_Reset = P2_7;
const int LoRa_IRQ = P2_6;
const int LoRa_DIO1 = P2_5;


const int ESP32Cam_OneWire = P2_4;

const int LSM6DSMTR_SCL = P4_7;
const int LSM6DSMTR_SDA = P4_6;

const int GPS_TX = P4_3;
const int GPS_RX = P4_2;
const int GPS_Enable = P2_3;

const int CamTrigServo_Trigger = P2_1;
const int CamTrigServo_Reload = P2_0;

const int ESP32Cam_Backup = P1_7;

const int CurrentSense = P5_3;
const int LightSense = P5_2;
const int Buzzer = P5_1;
const int BattVoltageSense = P5_0;

const int StatusLED1 = P3_3;
const int StatusLED2 = P3_2;
const int StatusLED3 = P3_1;

const int BattManage_5VEnable = P3_0;

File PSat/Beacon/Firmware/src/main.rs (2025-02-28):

#![no_main]
#![no_std]

use embedded_hal::{digital::v2::*, spi::MODE_0};
use embedded_hal_compat::{eh1_0::delay::DelayNs, ForwardCompat};
use embedded_lora_rfm95::{lora::types::{Bandwidth, CodingRate, CrcMode, HeaderMode, Polarity, PreambleLength, SpreadingFactor, SyncWord}, rfm95::{Rfm95Driver, RFM95_FIFO_SIZE}};
use msp430::critical_section;
use msp430_rt::entry;
use msp430fr2355::{E_USCI_A0, E_USCI_A1, P2};
use msp430fr2x5x_hal::{
    clock::{ClockConfig, DcoclkFreqSel, MclkDiv, SmclkDiv}, delay::Delay, fram::Fram, gpio::{Batch, Output, Pin, Pin0, Pin1, Pin2}, hal::blocking::delay::DelayMs, pmm::Pmm, serial::SerialConfig, spi::SpiBusConfig, watchdog::Wdt
};

use core::{cell::RefCell, panic::PanicInfo, str};
#[panic_handler]
fn panic_handler(panic_info: &PanicInfo) -> ! {
    msp430::interrupt::disable();
    println!("Panic: {:?}", panic_info);
    loop { msp430::asm::barrier(); }
}

/// Standard printing. Fails to print if SERIAL hasn't been configured yet.
#[macro_export]
macro_rules! println {
    ($first:tt $(, $( $rest:tt )* )?) => {
        {
            critical_section::with(|cs| {
                let Some(ref mut serial) = *$crate::SERIAL.borrow_ref_mut(cs) else {loop{}};
                use core::fmt::Write;
                writeln!(serial, $first,  $( $($rest)* )*).ok();
            });
        }
    };
}

use msp430::interrupt::Mutex;
static SERIAL: Mutex<RefCell<Option< MySerial >>> = Mutex::new(RefCell::new(None));

// Red onboard LED should blink at a steady period.
#[entry]
fn main() -> ! {
    // Take peripherals and disable watchdog
    let regs = msp430fr2355::Peripherals::take().unwrap();
    let _wdt = Wdt::constrain(regs.WDT_A);

    // Configure GPIO
    let pmm = Pmm::new(regs.PMM);
    let port2 = Batch::new(regs.P2).split(&pmm);

    let mut red_led = port2.pin0.to_output();
    let mut blue_led = port2.pin1.to_output();
    let mut green_led = port2.pin2.to_output();

    red_led.set_high().ok();
    blue_led.set_high().ok();
    green_led.set_high().ok();

    let port1 = Batch::new(regs.P1).split(&pmm);
    let port4 = Batch::new(regs.P4).split(&pmm);
    let port5 = Batch::new(regs.P5).split(&pmm);

    let mut lora_reset = port5.pin3.to_output(); // Not actually connected...
    lora_reset.set_high().ok();
    let miso = port4.pin7.to_alternate1();
    let mosi = port4.pin6.to_alternate1();
    let sclk = port4.pin5.to_alternate1();
    let mut cs = port4.pin4.to_output();
    cs.set_high().ok();

    let tx_pin = port1.pin7.to_alternate1();

    // Configure clocks to get accurate delay timing
    let mut fram = Fram::new(regs.FRCTL);
    let (smclk, _aclk, mut delay) = ClockConfig::new(regs.CS)
        .mclk_dcoclk(DcoclkFreqSel::_8MHz, MclkDiv::_1)
        .smclk_on(SmclkDiv::_1)
        .freeze(&mut fram);

    let spi = SpiBusConfig::new(regs.E_USCI_B1, MODE_0, true)
        .use_smclk(&smclk, 32)
        .configure_with_software_cs(miso, mosi, sclk);

    let serial = SerialConfig::new(regs.E_USCI_A0, 
        msp430fr2x5x_hal::serial::BitOrder::LsbFirst, 
        msp430fr2x5x_hal::serial::BitCount::EightBits, 
        msp430fr2x5x_hal::serial::StopBits::OneStopBit, 
        msp430fr2x5x_hal::serial::Parity::NoParity, 
        msp430fr2x5x_hal::serial::Loopback::NoLoop, 
        9600)
        .use_smclk(&smclk)
        .tx_only(tx_pin);

    critical_section::with(|cs| {
        SERIAL.replace(cs, Some(MySerial(serial)));
    });
    //use core::fmt::Write;
    //let mut serial = MySerial(serial);
    println!("Serial init");

    lora_reset.set_low().ok();
    delay.delay_ms(1);
    lora_reset.set_high().ok();
    delay.delay_ms(6);

    let mut rfm95 = Rfm95Driver::new(spi.forward(), cs.forward(), lora_reset.forward(), MyDelay(delay)).unwrap();
    println!("RFM95 config success!");

    delay.delay_ms(1000);

    let lora_config = embedded_lora_rfm95::lora::config::Builder::builder()
        .set_bandwidth(Bandwidth::B7_8) // lowest bandwidth == longest range
        .set_coding_rate(CodingRate::C4_8) // Maximum error correction
        .set_crc_mode(CrcMode::Disabled)
        .set_frequency(915_000_000.into()) // Hz
        .set_header_mode(HeaderMode::Explicit)
        .set_polarity(Polarity::Normal)
        .set_preamble_length(PreambleLength::L8)
        .set_spreading_factor(SpreadingFactor::S10) // High SF == Best range
        .set_sync_word(SyncWord::PRIVATE);
    rfm95.set_config(&lora_config).unwrap();

    
    /*
    loop {
        println!("Beginning transmission...");
        transmit(&mut rfm95, b"Hello world!");
        println!("Transmission complete.");
        delay.delay_ms(1000);
    }*/
    
    loop {
        println!("Beginning recieve...");
        let mut recieve_buf = [0u8; RFM95_FIFO_SIZE];
        let packet = recieve(&mut rfm95, &mut recieve_buf);
        println!("Recieve ended.");
        println!("Packet: {}", str::from_utf8(packet).unwrap());
    }
    idle_loop(red_led, green_led, blue_led, delay);
}

type HorribleEmbeddedHalCompatRFM95Type = Rfm95Driver<embedded_hal_compat::Forward<msp430fr2x5x_hal::spi::SpiBus<msp430fr2355::E_USCI_B1>>, embedded_hal_compat::Forward<Pin<msp430fr2355::P4, msp430fr2x5x_hal::gpio::Pin4, Output>, embedded_hal_compat::markers::ForwardOutputPin>>;

fn recieve<'b>(rfm95: &mut HorribleEmbeddedHalCompatRFM95Type, buf: &'b mut [u8; RFM95_FIFO_SIZE]) -> &'b [u8] {
    let size;
    'outer: loop {
        let max_timeout = rfm95.rx_timeout_max().unwrap();
        rfm95.start_rx(max_timeout).unwrap();

        
        'inner: loop {
            match rfm95.complete_rx(buf) {
                Ok(Some(n)) => {size = n; break 'outer;},
                Ok(None) => continue,
                Err(_) => break 'inner,
            };
        };

    }
    &buf[0..size]
}

fn transmit(rfm95: &mut HorribleEmbeddedHalCompatRFM95Type, data: &[u8]) {
    rfm95.start_tx(data).unwrap();
    let mut result = rfm95.complete_tx();
    while let Ok(None) = result {
        result = rfm95.complete_tx();
    }
}

fn idle_loop(mut red_led: Pin<P2, Pin0, Output>, mut green_led: Pin<P2, Pin2, Output>, mut blue_led: Pin<P2, Pin1, Output>, mut delay: Delay) -> ! {
    loop {
        const LED_DELAY_MS: u16 = 50; // ms
        // Returns a `Result` because of embedded_hal, but the result is always `Ok` with MSP430 GPIO.
        // Rust complains about unused Results, so we 'use' the Result by calling .ok()
        red_led.set_low().ok();
        delay.delay_ms(LED_DELAY_MS);

        green_led.set_low().ok();
        delay.delay_ms(LED_DELAY_MS);

        blue_led.set_low().ok();
        delay.delay_ms(LED_DELAY_MS);

        red_led.set_high().ok();
        delay.delay_ms(LED_DELAY_MS);

        green_led.set_high().ok();
        delay.delay_ms(LED_DELAY_MS);

        blue_led.set_high().ok();
        delay.delay_ms(LED_DELAY_MS);
    }
}
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

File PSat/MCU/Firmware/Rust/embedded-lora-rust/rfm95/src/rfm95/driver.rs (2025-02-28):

//! RFM95 driver for LoRa operations

use crate::lora::airtime;
use crate::lora::config::Config;
use crate::lora::types::*;
use crate::rfm95::connection::Rfm95Connection;
use crate::rfm95::registers::*;
use crate::rfm95::RFM95_FIFO_SIZE;
use core::cmp;
use core::fmt::{Debug, Formatter};
use core::time::Duration;
use embedded_hal::delay::DelayNs;
use embedded_hal::digital::OutputPin;
use embedded_hal::spi::SpiBus;

/// Raw SPI command interface for RFM95
pub struct Rfm95Driver<Bus, Select>
where
    Bus: SpiBus,
    Select: OutputPin,
{
    /// The SPI connection to the RFM95 radio
    spi: Rfm95Connection<Bus, Select>,
}
impl<Bus, Select> Rfm95Driver<Bus, Select>
where
    Bus: SpiBus,
    Select: OutputPin,
{
    /// Supported silicon revisions for compatibility check
    #[cfg(not(feature = "debug"))]
    const SUPPORTED_SILICON_REVISIONS: [u8; 2] = [0x11, 0x12];
    /// The frequency divider to compute the frequency in milli-hertz
    const FREQUENCY_DIVIDER_MILLIHZ: u64 = 61_035;
    /// The threshold for switching between low-frequency mode (below 525 MHz) and high frequency mode (above 779 MHz)
    const HIGH_FREQUENCY_THRESHOLD: Frequency = Frequency::hz(652_000_000);

    /// The register value to put the device to LoRa mode
    const REG_OPMODE_LONGRANGEMODE_LORA: u8 = 0b1;
    /// The register value to set the shared registers to LoRa mode
    const REG_OPMODE_ACCESSSHAREDREG_LORA: u8 = 0b0;
    /// The pre-assembled register value for the operation mode register to put the device to sleep
    const REG_OPMODE_MODE_SLEEP: u8 = 0b000;
    /// The pre-assembled register value for the operation mode register to go into standby during LoRa mode
    const REG_OPMODE_MODE_STANDBY: u8 = 0b001;
    /// The pre-assembled register value for the operation mode register to start a single LoRa TX transmission
    const REG_OPMODE_MODE_TXSINGLE: u8 = 0b011;
    /// The pre-assembled register value for the operation mode register to start a single LoRa RX reception
    const REG_OPMODE_MODE_RXSINGLE: u8 = 0b110;

    /// Creates a new raw SPI command interface for RFM95
    ///
    /// # Blocking
    /// This function blocks for at least `11ms` plus additional time for the modem transactions. If you have tight
    /// scheduling requirements, you probably want to initialize this driver before entering your main event loop.
    ///
    /// # Important
    /// The RFM95 modem is initialized to LoRa-mode and put to standby. All other configurations are left untouched, so
    /// you probably want to configure the modem initially (also see [`Self::set_config`]).
    pub fn new<R, T>(bus: Bus, select: Select, mut reset: R, mut timer: T) -> Result<Self, &'static str>
    where
        R: OutputPin,
        T: DelayNs,
    {
        // Pull reset to low and wait until the reset is triggered
        reset.set_low().map_err(|_| "Failed to pull reset line to low")?;
        timer.delay_ms(1);

        // Pull reset to high again and give the chip some time to boot
        reset.set_high().map_err(|_| "Failed to pull reset line to high")?;
        timer.delay_ms(10);

        // Validate chip revision to assure the protocol matches
        let mut wire = Rfm95Connection::init(bus, select);
        #[cfg(not(feature = "debug"))]
        {
            // Get chip revision
            let silicon_revision = wire.read(RegVersion)?;
            let true = Self::SUPPORTED_SILICON_REVISIONS.contains(&silicon_revision) else {
                // Raise an error here since other revisions may be incompatible
                return Err("Unsupported silicon revision");
            };
        }

        // Go to sleep, switch to LoRa and enter standby
        wire.write(RegOpModeMode, Self::REG_OPMODE_MODE_SLEEP)?;
        wire.write(RegOpModeLongRangeMode, Self::REG_OPMODE_LONGRANGEMODE_LORA)?;
        wire.write(RegOpModeMode, Self::REG_OPMODE_MODE_STANDBY)?;
        wire.write(RegOpModeAccessSharedReg, Self::REG_OPMODE_ACCESSSHAREDREG_LORA)?;

        // Set TX and RX base address to 0 to use the entire available FIFO space, and the power amplifier to max
        wire.write(RegFifoTxBaseAddr, 0x00)?;
        wire.write(RegFifoRxBaseAddr, 0x00)?;
        wire.write(RegPaConfig, 0xFF)?;

        // Init self
        Ok(Self { spi: wire })
    }

    /// Applies the given config (useful for initialization)
    pub fn set_config(&mut self, config: &Config) -> Result<(), &'static str> {
        self.set_spreading_factor(config.spreading_factor())?;
        self.set_bandwidth(config.bandwidth())?;
        self.set_coding_rate(config.coding_rate())?;
        self.set_polarity(config.polarity())?;
        self.set_header_mode(config.header_mode())?;
        self.set_crc_mode(config.crc_mode())?;
        self.set_sync_word(config.sync_word())?;
        self.set_preamble_len(config.preamble_len())?;
        self.set_frequency(config.frequency())?;
        Ok(())
    }

    /// The current spreading factor
    pub fn spreading_factor(&mut self) -> Result<SpreadingFactor, &'static str> {
        let spreading_factor = self.spi.read(RegModemConfig2SpreadingFactor)?;
        SpreadingFactor::try_from(spreading_factor)
    }
    /// Set the spreading factor
    pub fn set_spreading_factor<T>(&mut self, spreading_factor: T) -> Result<(), &'static str>
    where
        T: Into<SpreadingFactor>,
    {
        // Get config to determine the need for LDO
        let spreading_factor = spreading_factor.into();
        let bandwidth = self.bandwidth()?;
        let needs_ldo = airtime::needs_ldo(spreading_factor, bandwidth);

        // Set registers
        self.spi.write(RegModemConfig2SpreadingFactor, spreading_factor as u8)?;
        self.spi.write(RegModemConfig3LowDataRateOptimize, needs_ldo as u8)?;
        Ok(())
    }

    /// The current bandwidth
    pub fn bandwidth(&mut self) -> Result<Bandwidth, &'static str> {
        let bandwidth = self.spi.read(RegModemConfig1Bw)?;
        Bandwidth::try_from(bandwidth)
    }
    /// Sets the bandwidth
    pub fn set_bandwidth<T>(&mut self, bandwidth: T) -> Result<(), &'static str>
    where
        T: Into<Bandwidth>,
    {
        // Get config to determine the need for LDO
        let bandwidth = bandwidth.into();
        let spreading_factor = self.spreading_factor()?;
        let needs_ldo = airtime::needs_ldo(spreading_factor, bandwidth);

        // Set registers
        self.spi.write(RegModemConfig1Bw, bandwidth as u8)?;
        self.spi.write(RegModemConfig3LowDataRateOptimize, needs_ldo as u8)?;
        Ok(())
    }
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

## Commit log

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2024-03-12 PSU v2.0.1
    Add custom parameter 'version' to automatically update on schematics and PCBs. Accessed through Project > Project Options > Parameters.
    Add thermal reliefs to ABF header
    [Battery charger.SchDoc, Main.SchDoc, PSU.PcbDoc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]
2024-03-12 Update payload template
    Add optional additional headers, also fix missing libraries
    [Payload.PcbDoc, Payload.PrjPcb, Payload.SchDoc]
2024-03-12 Fix beacon libraries
    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
    [Beacon.PcbDoc, Beacon.SchDoc, PSat Generic Beacon.PrjPcb]
2024-03-12 Add versioning to MCU
    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
    [MCU.PcbDoc, MCU.SchDoc, PSat Generic MCU.PrjPcb]
2024-03-12 Rename projects
    Remove 'generic' from project names, it just gets in the way
    [PSat Beacon.PrjPcb, PSat MCU.PrjPcb, PSat PSU.PrjPcb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]
2024-03-14 PSU 2.0.2
    Mostly documentation.
    Add resistor relationships to converter schematics.
    Modify payload disable pulldown from 100k -> 10k to reduce unique part count
    Reposition version string slightly
    Add IsInLabBook marker to passive components
    Move ABF header so that battery can be charged while ABF disconnected
    [Battery charger.SchDoc, Main.SchDoc, PSU.PcbDoc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]
2024-03-14 MCU Fix BoM
    Fix some unnecessary components appearing in the BoM.
    [MCU.SchDoc]
2024-03-17 Bugfix: Convert special strings
    Altium17 doesn't automatically convert special strings on the PCB. Used for the version string.
    [Beacon.PcbDoc, MCU.PcbDoc]
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2024-03-17 Beacon: Move 3V3 track on bottom so it's not cutting off ground
    [Beacon.PcbDoc]
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2024-03-17 Bugfix: Move solder bridge components on-grid
    [Beacon.PcbDoc, Beacon.SchDoc, MCU.PcbDoc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]
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2024-03-22 Move common libraries to shared folder
    Added symlink to each project folder, might be a bit more robust than linking to the external shared lib through Altium?
    [General Components.PcbLib, General Components.SchLib, JellybeanComponents.PcbLib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]
2024-03-22 PSU 2.0.3: Switch to Remove Before Flight connector
    Due to popular demand
    [Main.SchDoc, PSU.PcbDoc, PSat PSU.PrjPcb]
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2024-04-09 Refactor adapter boards
    Add SOT-323 to SOT-23,SOT-28 board.
    Move SOD-123 to a new board with SOD-323 and resistor/capacitor footprints.
    [0805,0603,0402,SOD-123,SOD-323.PrjPcb, PCB.PcbDoc, SOT-23,SOT-28,SOT-323.PrjPcb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]
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2024-04-20 Update standard parts libraries
    Added most prototyping parts. Still need to do passives and a few other parts like crystals.
    Updated resistors footprints in flight parts
    [APSS Flight Parts.PcbLib, APSS Flight Parts.SchLib, APSS Prototype Parts.PcbLib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]
2024-04-21 Update libraries
    Add picoblade headers (still misisng footprints), some parameters, update wrong MSOP footprint
    [APSS Flight Parts.PcbLib, APSS Flight Parts.SchLib, APSS Prototype Parts.PcbLib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]
2024-04-21 Breadboard adapters: Square pins only on pin 1
    Making it clearer where pin 1 is
    [PCB.PcbDoc]
2024-04-21 Breadboard adapters: Add 0.5mm MSOP
    Combined SOIC with the 0.65mm pitch chips to make room for a 0.5mm MSOP footprint
    [PCB.PcbDoc, Schematic.SchDoc]
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2024-04-21 Standard libraries: Reduce solder mask expansion for small pitch ICs
    4mil -> 2mil, will hopefully mean we get some solder mask between pins to make soldering easier.
    [APSS Prototype Parts.PcbLib, APSS Prototype Parts.SchLib]
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2024-04-22 Standard libraries: Add digikey part numbers
    Also fix some typos
    [APSS Flight Parts.SchLib, APSS Prototype Parts.PcbLib, APSS Prototype Parts.SchLib]
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2024-04-22 Standard libraries: Fix typos, add voltage ratings for ICs
    [APSS Flight Parts.SchLib, APSS Prototype Parts.SchLib]
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2024-04-23 MCU 2.0.1: Add Spy-Bi-Wire programming interface as nested footprint
    The original 8-wire picoclasp header has been replaced with the 8-wire picoblade, which has a 4-wire SBW picoblade nested inside it, which has a 2-pin 2.54mm header inside that, for 'manual' programming
    Add warning regarding maximum battery voltage sampling rate
    [MCU.PcbDoc, MCU.SchDoc, PPCB_Programming_Adaptor.PrjPcb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]
2024-04-24 Update shared libraries, new readme
    Old readme moved to PSat folder.
    Update general components library to contain generic components and test points, solder jumpers, etc.
    [General Components.PcbLib, General Components.SchLib, JellybeanComponents.PcbLib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]
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2024-04-25 Add multifunction logic gate 74LVC1G97W6-7, update footprints
    Make pin 1 dot smaller and move out of the way more. Add dots between pads of 0402 parts, etc.
    [APSS Prototype Parts.PcbLib, APSS Prototype Parts.SchLib]
2024-05-04 Completed odd numbered pin headers
    Added schematic symbol and footprint for all odd numbered pin headers - TH (STR and RA) and SMD (STR and RA)
    [APSS Flight Parts.SchLib]
2024-05-04 Add footprints and models for even SMT headers
    Also fix 3d model colours
    [APSS Flight Parts.SchLib]
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2024-05-05 Shared libraries: QoL updates
    Move designators, resistors get tolerance on footprint, tidy up, etc.
    [APSS Flight Parts.SchLib, APSS Prototype Parts.SchLib]
2024-05-05 PSU 2.0.4: Use APSS standard parts libraries, add solder jumpers
    Solder jumpers for supply control, in case S1 isn't populated.
    [Battery charger.SchDoc, Main.SchDoc, PSU.PcbDoc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]
2024-05-05 Fix library footprint linking, move PCBway rules file to shared
    Some of the prototype symbols were linking to flight footprints and vice versa.
    Add molex headers to prototype library.
    Update and move PCBway rules file to shared folder.
    TODO: Update and move outjob to shared folder after moving other PCBs to shared libraries.
    TODO: Figure out exactly what the 'comment' field should contain. Part number? Value? A bit of both?
    [APSS Flight Parts.SchLib, APSS Prototype Parts.SchLib, General Components.PcbLib]
2024-05-05 MCU 2.0.2: Use shared libraries
    Still using an old library for the MSP. Too much hassle to swap it over.
    [MCU.PcbDoc, MCU.SchDoc, PSat MCU.PrjPcb]
2024-05-08 Align general + prototype components to 100mil grid
    Also try to leave 400mil spacing (i.e. 1 passive) between pins that often have a passive between them
    Flight parts TODO
    [APSS Prototype Parts.SchLib, General Components.SchLib]
2024-05-09 Fixing MP2 designator for all headers
    MP2 pin for the molex headers had the correct name but the designator was still MP1 - fixed this error.
    [APSS Flight Parts.SchLib]
2024-05-09 Fixing MP2 designators for headers in the prototype library
    Previous commit only fixed the designators for the flight-ready library. This commit fixes the issue in the prototype library.
    [APSS Prototype Parts.SchLib]
2024-05-09 Added schematic symbol for crystals
    Added two schematic symbols for crystals - one in the flight and one in the prototype library.
    [APSS Flight Parts.SchLib, APSS Prototype Parts.SchLib]
2024-05-09 Align flight parts and general components to 100mil grid
    Also centre footprints, except molex headers
    [APSS Flight Parts.SchLib, General Components.PcbLib]
2024-05-11 Fix ADC part number
    [APSS Flight Parts.SchLib]
2024-05-17 Fix 'Silk to Solder Mask' Warnings on Picoblade Footprints
    Also add JTAG header to prototype parts library
    [APSS Prototype Parts.SchLib]
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2024-05-20 Libraries: Fix solder bridge footprints to allow snapping to pads
    [General Components.PcbLib]
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2024-05-22 Update breadboard footprints with .RUL file
    Also misc adjustments to solve warnings
    [0805,0603,0402,SOD-123,SOD-323.PrjPcb, PCB.PcbDoc, SOT-223,0606,0603.PrjPcb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]
2024-05-22 MCU: Fix small capacitor footprints
    Remove 0402 caps accidentally added during library transition from board to ease soldering.
    [MCU.PcbDoc, MCU.SchDoc, PSat MCU.PrjPcb]
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2024-05-22 MCU: Fix 100nF capacitor part number
    [MCU.SchDoc]
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2024-05-30 PSU: Prepare for printing
    Move L1 away from hole, make holes on the header plated in case we want to use them bare.
    PSU
    [Battery charger.SchDoc, Main.SchDoc, PSU.PcbDoc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]
2024-05-30 Beacon: Prepare for printing
    Reduce silk-solder mask errors, etc.
    Beacon
    [Beacon.PcbDoc, PSat Beacon.PrjPcb]
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2024-06-06 Add board outline clearance to cheap PCB rules
2024-06-10 Libraries: Remove expensive caps from prototyping, add cheaper ones
    Also update resistor/capacitor symbols to show tolerance based on the Tolerance parameter
    [APSS Flight Parts.SchLib, APSS Prototype Parts.SchLib, General Components.SchLib]
2024-06-10 PCBs: Update schematic symbols from libraries
    Also update outjobs to make them more sane. Probably time to make a generic outjob file to go in the shared libs folder.
    Beacon PCB v2.0.1: Add a decoupling cap to the 555 timer per datasheet
    PSU v2.0.5: Add an extra smoothing cap to the PSU 5V rail as per datasheet
    [Battery charger.SchDoc, Beacon.PcbDoc, Beacon.SchDoc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]
2024-06-11 Add generic outjob file to shared libraries folder
    Also update outjobs to match.
    Update descriptions in general components library to better match the other APSS libraries
    [General Components.SchLib]
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2024-06-26 Beacon: Fix top solder paste on LoRA127X-C1 footprint
    Solder paste was on top of solder mask.
    Currently the pad is longer than the solder mask cutout because the module has holes near the edge as well as castellated edges. I don't want solder from the hole going down to the pad, as it could make desoldering tricky.
    Maybe I should just make the pads smaller?
    [Beacon.PcbDoc]
2024-06-28 fix: Wrong designator for 2pin molex in Prototype PCBLib
2024-06-29 Fix wrong pin designators for 2-pin flight header
2024-09-22 MCU Errata: Update resistor values, add SBW note
    Confirmed that both 2-pin and 4-pin programming works. Had issues with the reset cap on 2-wire though.
    Add note about 1nF capacitor potentially interfering with SBW programming
    Change reset pin pullup from 4.7k to 47k, as specified in the datasheet (whoops)
    Change 100k battery divider resistors to 47k to consolidate with reset pullup
    [MCU.SchDoc]
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2024-10-04 Add WIP pogo pin layout to programming adapter board
    Also modify pin layout to disambiguate flipped layouts (i.e. bottom layer), and add silkscreen/courtyard.
    [General Components.PcbLib, General Components.SchLib, PPCB_Programming_Adaptor.PrjPcb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]
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2024-10-09 Libraries: Fix capacitor footprint parameters
    GRM21BR61C226ME44L, C0805C226M9PACTU were labelled as 0402 instead of 0805.
    [APSS Prototype Parts.SchLib]
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2024-10-15 Libraries: AB30S SSR, TMP1075 temp sensors, BQ21040DBVR battery charger
    Also adjust AB30S-Q-R1 from Flight Parts library to make the courtyard the correct size.
    [APSS Prototype Parts.SchLib]
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2024-11-03 Prog adapter: Fix board outline
    [Prog_Adaptor.PcbDoc]
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2024-11-24 Update rules file to add hole clearance constraints
    For whatever reason the hole clearances were zeroed out
    [Beacon.PcbDoc, MCU.PcbDoc, PSU.PcbDoc]
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2024-11-27 Component errors fixed
    [Motherboard.PcbDoc, Motherboard.SchDoc, QSatMotherboard.PrjPcb]
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2024-11-29 Added missing component to PCB
    [Motherboard.PcbDoc]
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2024-12-06 PSU v2.0.6
    Add more comments to top level schematic. Fix BOM entries. Increase size of plating around holes. Change documentation from 'attach before flight' to 'remove before flight' to mirror the actual functionality.
    [Battery charger.SchDoc, Main.SchDoc, PSU.PcbDoc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]
2024-12-06 Beacon v2.0.2
    Fix BOM. Expand pads around mounting holes. Fix 3-way solder bridge spurious solder mask sliver warnings. Add silk screen to generic 0402 resistor footprint
    [APSS Generic Components.PcbLib, Beacon.PcbDoc, Beacon.SchDoc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]
2024-12-06 Payload Template: Use non-overlapping headers
    The headers themselves are the same, but the footprint in Altium is reduced to prevent spurious warnings.
    Also disable rooms in project, and add net labels to pads used in other reference boards
    [APSS Generic Components.PcbLib, APSS Generic Components.SchLib, Payload.PcbDoc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]
2024-12-07 Supplier Part No. Fix for Headers
    Fixing some of the header components in both Flight Parts and Prototype Parts libraries by updating the 'supplier part no.' field (was previously MPN not the digikey no.)
    [APSS Flight Parts.SchLib, APSS Prototype Parts.SchLib]
2024-12-10 Add reference board errata
2024-12-10 Beacon v2.0.3: Documentation update
    Version bump. Fix documentation error
    [Beacon.PcbDoc, Beacon.SchDoc, PSat Beacon.PrjPcb]
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2025-01-30 Revert USB-C header, new SMT version. Add IMU
    Through-hole one violates rules :(
    New SMT version has longer legs, can do 1.6mm PCBs
    [APSS Prototype Parts.SchLib]
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2025-02-26 Set sensible defaults, add radio range test fns
    Also rename internals to 'driver' to avoid `board.radio.radio`
    [board.rs, lora.rs]
2025-02-27 Bugfixes
    Remove panic handler serial reconfiguration. Seems to cause weird bugs: Freezes after initial clock selection. TODO.
    Do serial configuration as early as possible.
    Add relative timestamps to tx range test.
    Add padding to timestamps
    [board.rs, lora.rs]
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2025-03-05 Fix servos
2025-03-05 changed some code and it didn't work last time idk why (works now)
    [main.cpp]
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
